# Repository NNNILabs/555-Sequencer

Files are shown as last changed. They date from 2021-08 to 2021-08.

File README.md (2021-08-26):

# 555-Sequencer
## Sequencer board for the railgun

PCBs for this project were sponsored by [JLCPCB]( https://jlcpcb.com/RHG).

This board was designed with simplicity in mind - you could almost say that I predicted the 2020/2021 chip shortage. The original railgun controller board was based on an STM32 board, but issues with code delivery prompted me to try a simpler alternative. 

The board can roughly be divided into three blocks - the power supply, the toggle latch and the sequencer.

The power supply is based around the classic 78L05 linear regulator, and can handle input voltages up to 30V. 

The toggle latch 555 timer switches the output between high and low every time the switch is pressed. Initially, when the board is powered on, the output is low thanks to the RC delay on the reset pins. when the switch is pressed, pin 2 detects that the capacitor is uncharged and sets the output high. The capacitor now charges through the resistor and goes high. When the button is pressed again, pin 6 detects that the capacitor is charged and the output is set low. The output of the toggle 555 connects to the LT3750 based capacitor charger, which needs a rising edge to trigger the charging process. 

The next 3 555 timers form a sequencer. The first 555 timer is triggered by the falling edge of the toggle 555 timer and outputs a 10us pulse. The falling edge of this 10us pulse triggers the second 555 to output a pulse of 100us, which again triggers the third 555 to output a 10us pulse. The outputs of the first and third timers in the sequencer form the 10us gate drive pulses for the SCRs, spaced 100us apart. 

This whole configiration needs only one switch to operate - press once to charge, press a second time to fire.

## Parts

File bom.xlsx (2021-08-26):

Designator | Comment | Footprint |  |  | JLCPCB Part #
C1, C15 | 1uF | Capacitor_SMD:C_0603_1608Metric | ~ | 2 | C15849
C2, C4, C6 | 1nF | Capacitor_SMD:C_0603_1608Metric | ~ | 3 | C1588
C3, C5, C7 | 10nF | Capacitor_SMD:C_0603_1608Metric | ~ | 3 | C57112
C8-C13 | 100nF | Capacitor_SMD:C_0603_1608Metric | ~ | 6 | C14663
D1, D2 | 4148 | Diode_SMD:D_SOD-323 | ~ | 2 | C2128
J1 | IO | Connector_PinSocket_2.54mm:PinSocket_2x05_P2.54mm_Vertical | ~ | 1
R1, R3, R4, R13 | 100K | Resistor_SMD:R_0603_1608Metric | ~ | 4 | C25803
R5, R8, R9, R11, R14 | 10K | Resistor_SMD:R_0603_1608Metric | ~ | 5 | C25804
R6, R12 | 1K | Resistor_SMD:R_0603_1608Metric | ~ | 2 | C21190
U1-U4 | TLC555xD | Package_SO:SOIC-8_3.9x4.9mm_P1.27mm | http://www.ti.com/lit/ds/symlink/tlc555.pdf | 4 | C6986
U5 | L78L05 | Package_TO_SOT_SMD:SOT-89-3 | http://www.st.com/content/ccc/resource/technical/document/datasheet/15/55/e5/aa/23/5b/43/fd/CD00000446.pdf/files/CD00000446.pdf/jcr:content/translations/en.CD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 | 1 | C71136

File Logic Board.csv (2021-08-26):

Comment | Designator | Footprint | LCSC Part #
1uF Unpolarized capacitor | C1,C15 | C_0603_1608Metric | C15849
1nF Unpolarized capacitor | C2,C4,C6 | C_0603_1608Metric | C1588
10nF Unpolarized capacitor | C3,C5,C7 | C_0603_1608Metric | C57112
100nF Unpolarized capacitor | C8,C9,C10,C11,C12,C13 | C_0603_1608Metric | C14663
4148 Diode | D1,D2 | D_SOD-323 | C2128
IO Generic connector, double row, 02x05, odd/even pin numbering scheme (row 1 odd numbers, row 2 even numbers), script generated (kicad-library-utils/schlib/autogen/connector/) | J1 | PinSocket_2x05_P2.54mm_Vertical
100K Resistor | R1,R3,R4,R13 | R_0603_1608Metric | C25803
10K Resistor | R5,R8,R9,R11,R14 | R_0603_1608Metric | C25804
1K Resistor | R6,R12 | R_0603_1608Metric | C21190
TLC555xD Single LinCMOS Timer, 555 compatible, SOIC-8 | U1,U2,U3,U4 | SOIC-8_3.9x4.9mm_P1.27mm | C6986
L78L05 Positive 100mA 30V Linear Regulator, Fixed Output 5V, SOT-89 | U5 | SOT-89-3 | C71136

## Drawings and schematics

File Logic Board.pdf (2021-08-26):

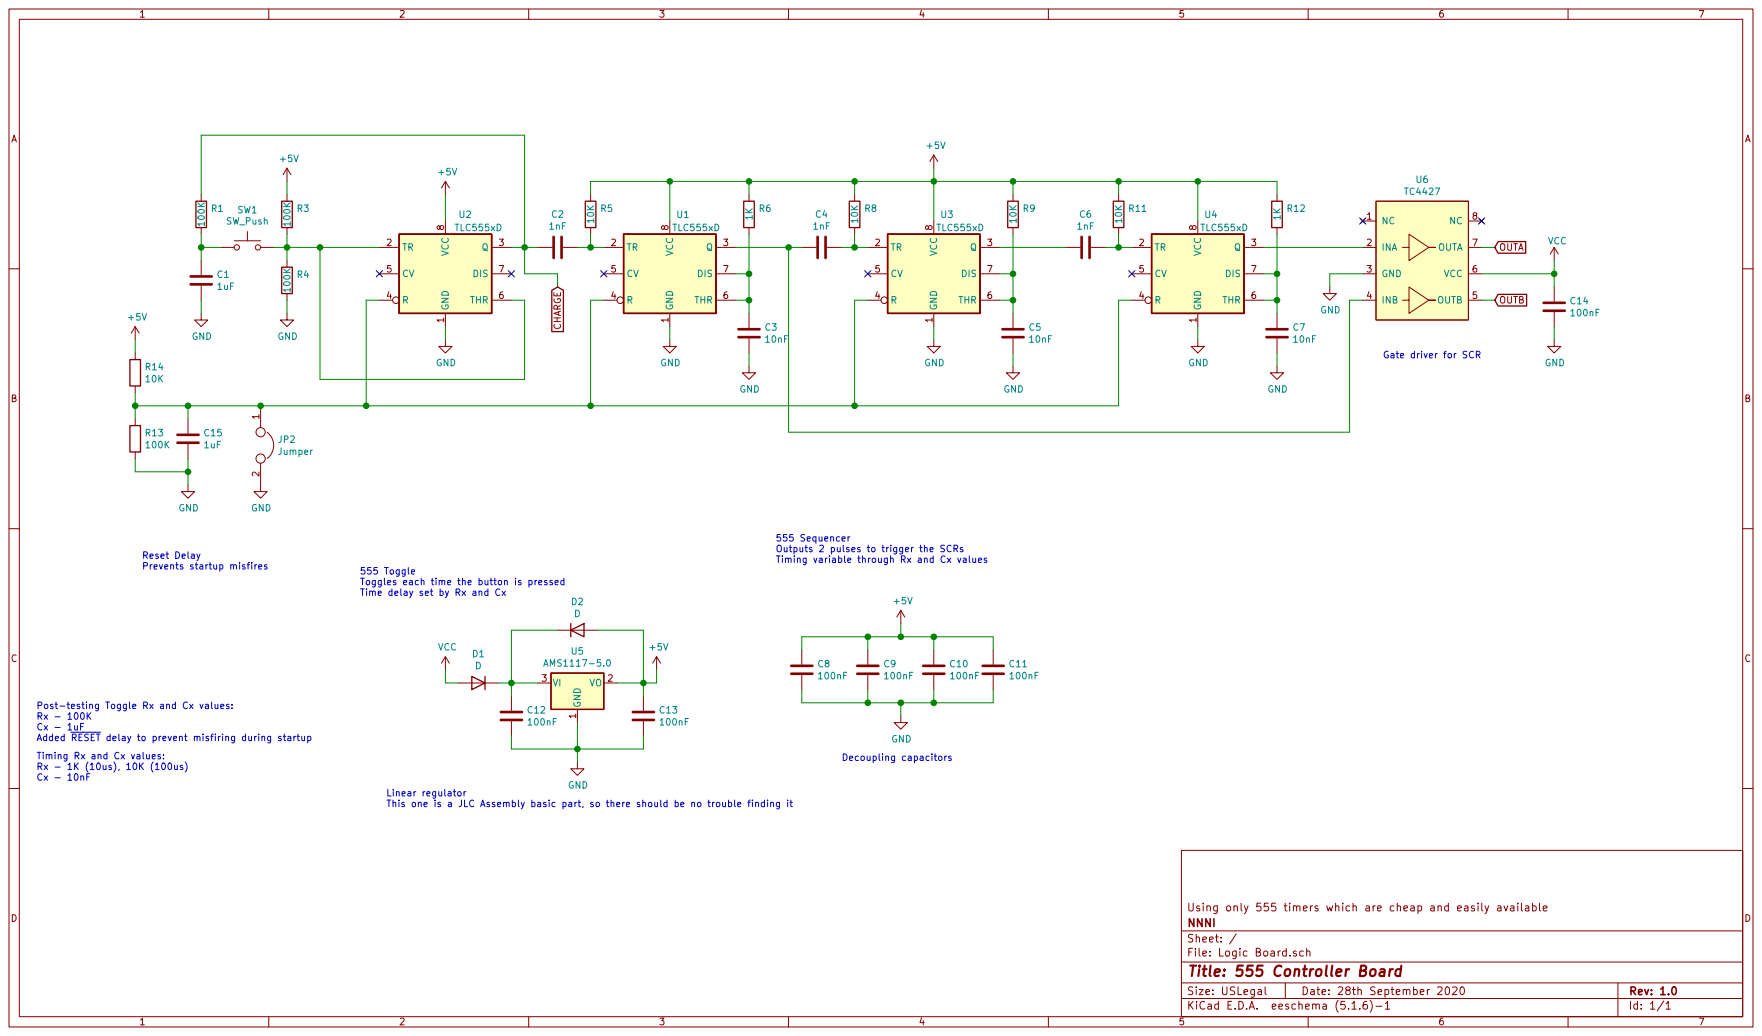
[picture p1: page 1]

555 Sequencer
Outputs 2 pulses to trigger the SCRs
Timing variable through Rx and Cx values

555 Toggle
Toggles each time the button is pressed
Time delay set by Rx and Cx

Linear regulator
This one is a JLC Assembly basic part, so there should be no trouble finding it

File: Logic Board.sch Sheet: / NNNI Using only 555 timers which are cheap and easily available

Id: 1/1 Title: 555 Controller Board
KiCad E.D.A. eeschema (5.1.6)-1

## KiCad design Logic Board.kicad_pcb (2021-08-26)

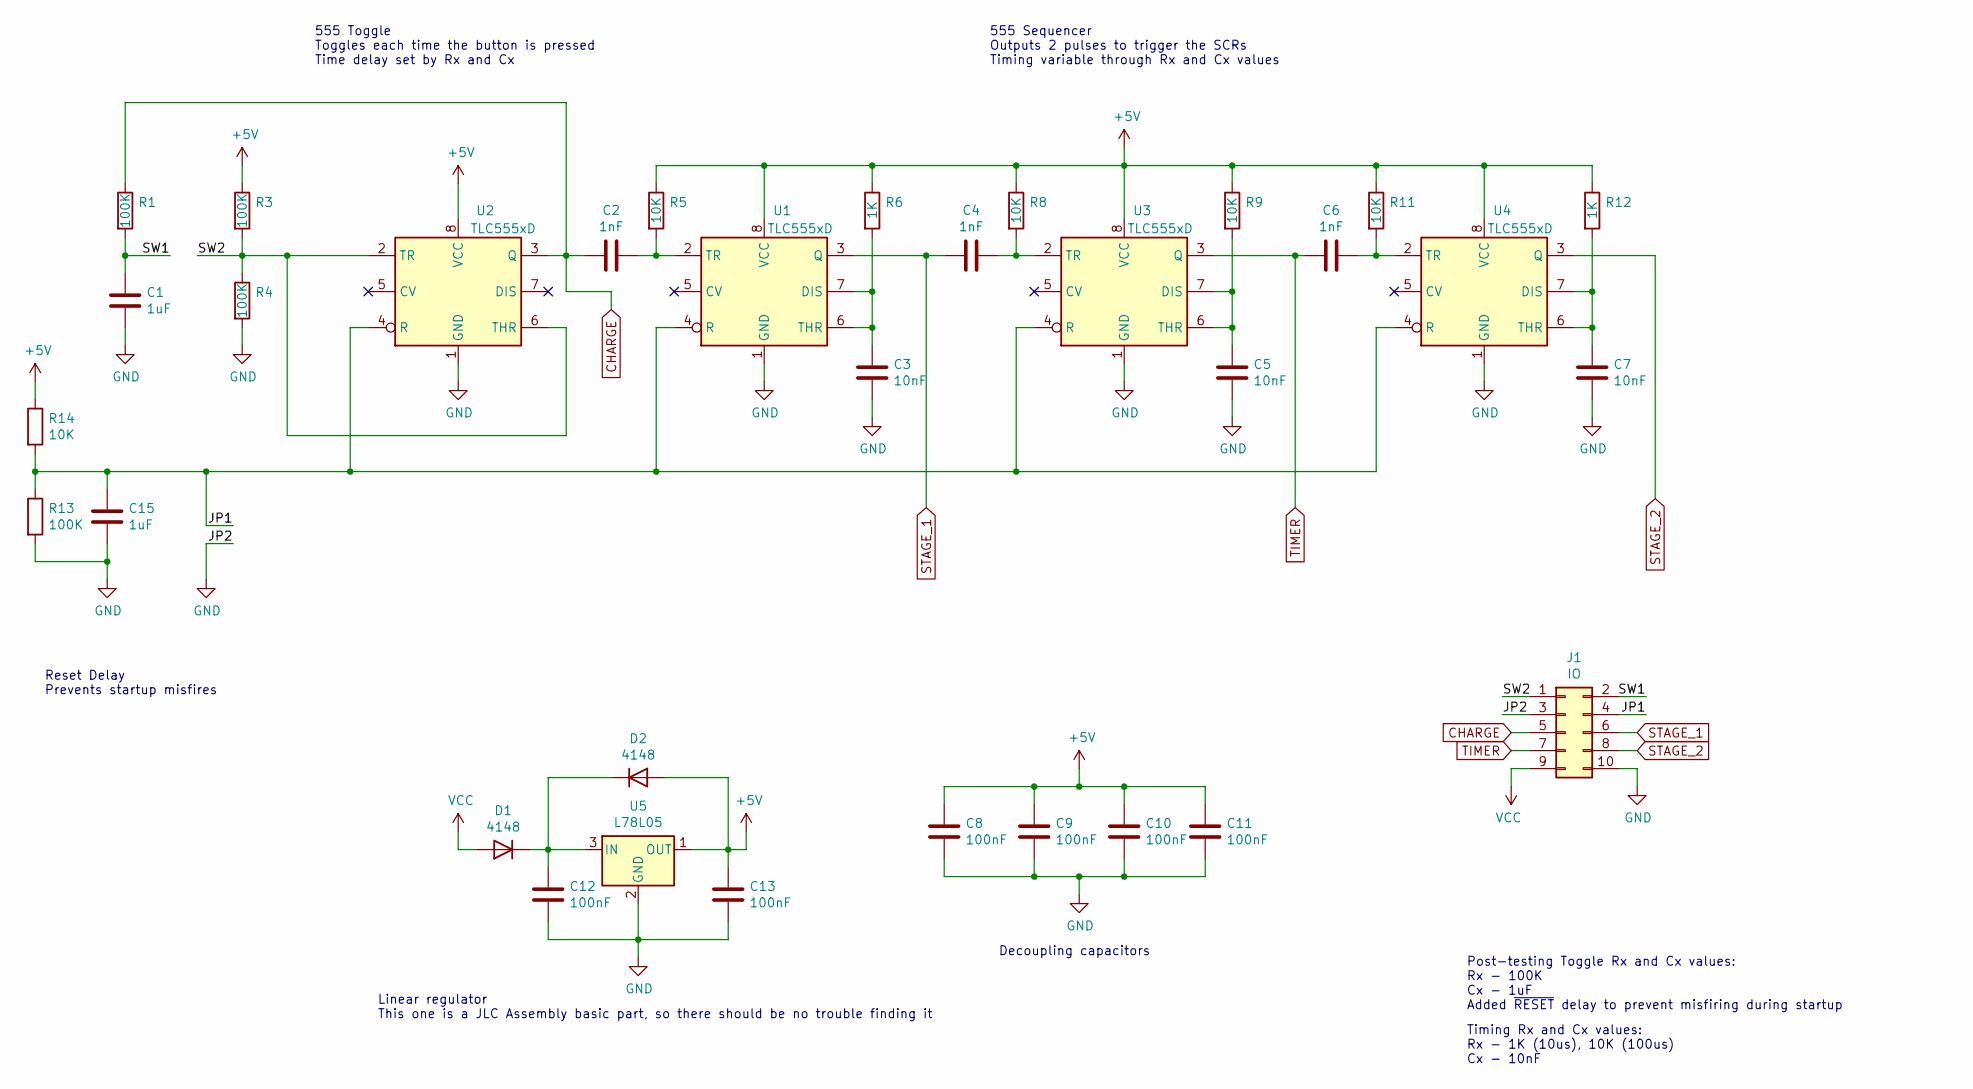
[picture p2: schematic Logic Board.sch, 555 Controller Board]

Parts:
C1, C15: 1uF; C_0603_1608Metric
C2, C4, C6: 1nF; C_0603_1608Metric
C3, C5, C7: 10nF; C_0603_1608Metric
C8, C9, C10, C11, C12, C13: 100nF; C_0603_1608Metric
D1, D2: 4148; D_SOD-323
J1: IO; PinSocket_2x05_P2.54mm_Vertical
R1, R3, R4, R13: 100K; R_0603_1608Metric
R5, R8, R9, R11, R14: 10K; R_0603_1608Metric
R6, R12: 1K; R_0603_1608Metric
U1, U2, U3, U4: TLC555xD; SOIC-8_3.9x4.9mm_P1.27mm
U5: L78L05; SOT-89-3

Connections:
+5V: C8.1, C9.1, C10.1, C11.1, C13.1, D2.2 (A), R3.1, R5.1, R6.1, R8.1, R9.1, R11.1, R12.1, R14.1, U1.8 (VCC), U2.8 (VCC), U3.8 (VCC), U4.8 (VCC), U5.1 (OUT)
/JP1: C15.1, J1.4, R13.1, R14.2, U1.4 (R), U2.4 (R), U3.4 (R), U4.4 (R)
/SW1: C1.1, J1.2, R1.2
/SW2: J1.1, R3.2, R4.1, U2.2 (TR), U2.6 (THR)
CHARGE: C2.2, J1.5, R1.1, U2.3 (Q)
GND: C1.2, C3.2, C5.2, C7.2, C8.2, C9.2, C10.2, C11.2, C12.2, C13.2, C15.2, J1.3, J1.10, R4.2, R13.2, U1.1 (GND), U2.1 (GND), U3.1 (GND), U4.1 (GND), U5.2 (GND)
unnamed: C2.1, R5.2, U1.2 (TR)
unnamed: C3.1, R6.2, U1.6 (THR), U1.7 (DIS)
unnamed: C4.1, R8.2, U3.2 (TR)
unnamed: C5.1, R9.2, U3.6 (THR), U3.7 (DIS)
unnamed: C6.1, R11.2, U4.2 (TR)
unnamed: C7.1, R12.2, U4.6 (THR), U4.7 (DIS)
unnamed: C12.1, D1.1 (K), D2.1 (K), U5.3 (IN)
STAGE_1: C4.2, J1.6, U1.3 (Q)
STAGE_2: J1.8, U4.3 (Q)
TIMER: C6.2, J1.7, U3.3 (Q)
VCC: D1.2 (A), J1.9

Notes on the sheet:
555 Sequencer Outputs 2 pulses to trigger the SCRs Timing variable through Rx and Cx values
555 Toggle Toggles each time the button is pressed Time delay set by Rx and Cx
Decoupling capacitors
Linear regulator This one is a JLC Assembly basic part, so there should be no trouble finding it
Post-testing Toggle Rx and Cx values: Rx - 100K Cx - 1uF Added ~RESET~ delay to prevent misfiring during startup
Timing Rx and Cx values: Rx - 1K (10us), 10K (100us) Cx - 10nF
Reset Delay Prevents startup misfires

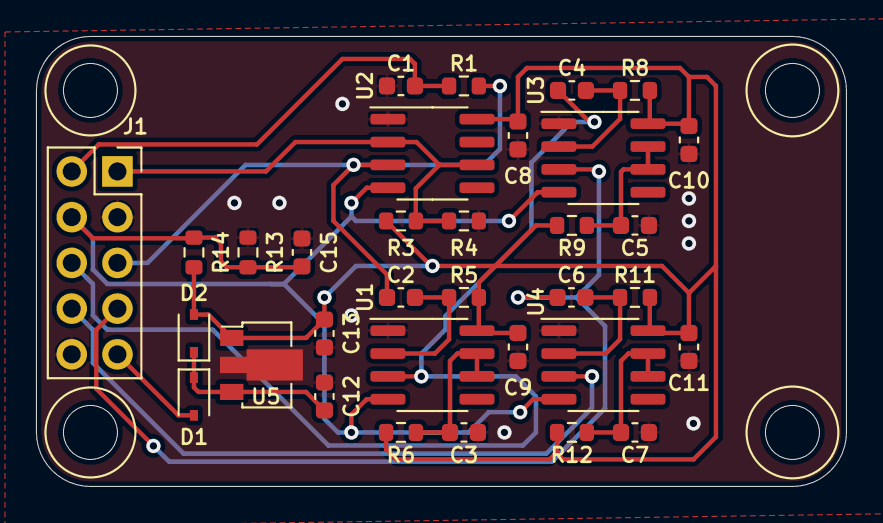
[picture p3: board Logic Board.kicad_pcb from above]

Board: 2 copper layers, 45.0 x 25.0 mm, 33 parts (0 on the bottom side), 17 nets.
